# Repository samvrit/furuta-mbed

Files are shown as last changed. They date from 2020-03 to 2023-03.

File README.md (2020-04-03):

# Double Furuta Pendulum
The Furuta pendulum experiment is one that is used to teach advanced control theory concepts. The goal is to balance pendulum bar(s) upright by actuating a motor at the base.



This is a continuation of my masters' thesis project on the same topic, which can be found [here](https://drum.lib.umd.edu/bitstream/handle/1903/21255/Srinivas_umd_0117N_19182.pdf?sequence=1&isAllowed=y)

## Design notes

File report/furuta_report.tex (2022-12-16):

\documentclass{report}

\usepackage{geometry}
\usepackage{amsmath}
\usepackage{graphicx}
\usepackage{url}

\renewcommand{\bibname}{References}

\graphicspath{ {./images/} }

\title{Furuta Pendulum Control Project Report}

\author{Samvrit Srinivas}

\date{\today}

\begin{document}

\maketitle

\chapter{Motor Controller} \label{chap:motor_controller}

The input for the furuta pendulum is a torque applied by the motor at the base of the setup. The high-level controller computes the amount of torque to be applied by the motor, and the low-level controller runs a PI control on the torque reference. We use a DC brushed motor for this purpose, and hence the motor controller is designed to be a current controller, as the torque is directly proportional to the winding current. The winding current is controlled by applying a pulse-width-modulated voltage at the motor terminals. In the following sections, we will look into the mathematical model and the control design of the current/torque controller.

\section{Motor Selection and Parameter Derivation}	\label{sec:motor_selection}
By simulating the high level controller with slightly different initial conditions, we were able to get an idea of the torque and speed requirements of the DC motor. A motor with a stall-torque rating of at least 4 Nm and a speed rating of at least 60 RPM was deemed necessary. A motor from Pololu was selected with the nameplate specifications shown in Table \ref{table:pololu_specs} \cite{pololu_motor_specs}.

\begin{table}
\begin{center}
\begin{tabular}{|c|c|}
\hline
\textbf{Parameter} & \textbf{Value }\\
\hline\hline
Voltage & 12V \\
\hline
No-load speed & 67 RPM \\
\hline
No-load current & 0.2 A \\
\hline
Stall torque & 4.9 Nm \\
\hline
Stall current & 5.5 A \\
\hline
\end{tabular}
\caption{Pololu motor nameplate specifications} \label{table:pololu_specs}
\end{center}
\end{table}

From the nameplate specifications and from CAD drawings provided by the manufacturer, the other motor parameters were derived, as shown in Table \ref{table:pololu_motor_params}.

\begin{table}
\begin{center}
\begin{tabular}{|c|c|c|}
\hline
\textbf{Parameter} & \textbf{Value} & \textbf{Units} \\
\hline \hline
$K_t$ & $0.968$ & $Nm/A$ \\
\hline
$K_v$ & $1.7103$ & $V/rad/s$ \\
\hline
$L$ & $2.3e-3$ & $H$ \\
\hline
$R$ & $2.18$ & $\Omega$ \\
\hline
$J$ & $12e-9$ & $kgm^2$ \\
\hline
$b$ & $0.0151$ & $Nm/rad/s$ \\
\hline
\end{tabular}
\caption{Motor parameters} \label{table:pololu_motor_params}
\end{center}
\end{table}

\subsection{Parameter Derivations}

\subsubsection{Torque Constant ($K_t$)}
\begin{equation}
K_t = \frac{\text{stall-torque}}{\text{stall-current}}
\end{equation}

\subsubsection{Back-EMF Constant ($K_v$)}
\begin{equation}
K_v = \frac{\text{nameplate voltage}}{\text{nameplate speed}}
\end{equation}

\subsubsection{Winding Inductance ($L$) and Resistance ($R$)}
\begin{equation}
R = \frac{\text{nameplate voltage}}{\text{stall current}}
\end{equation}
The inductance was provided by the manufacturer. It is also possible to measure the inductance using an LCR meter.

\subsubsection{Rotor Inertia ($J$)}
From the CAD model, the dimensions (volume and length) of the rotor were obtained. Assuming that the rotor is made of stainless steel, and using the density for stainless steel as $\rho = 7,500 kg/m^3$, the mass was determined. Using mass and length, the rotor inertia was estimated using
\begin{equation}
J = \frac{1}{12} \cdot m \cdot l^2
\end{equation}

\subsubsection{Coefficient of Viscous Friction ($b$)}
\begin{equation}
b = \frac{\text{no-load-current} \cdot K_t}{\text{no-load-speed}}
\end{equation}

\section{Mathematical Model of DC Motor}	\label{sec:math_model}

Since the winding current is controlled by applying a certain voltage at the motor terminals, it is beneficial to look at the transfer function $\frac{I(s)}{V(s)}$. Figure \ref{fig:dc_motor_transfer_fn} represents the current-voltage dynamics of a DC motor \cite{motor_control_umich_lecture}:\\

\begin{figure}[h]
\centering
	
\caption{Motor transfer function}
\label{fig:dc_motor_transfer_fn}
\end{figure}

The combined transfer function is as follows:

\begin{align}
\frac{I\left(s\right)}{V\left(s\right)} &= \frac{sJ + b}{(sL + R)\cdot(sJ + b) + K_t \cdot K_v} \label{eq:motor_plant_transfer_fn} \\
\nonumber \\
\text{where,} \nonumber \\
I(s) &= \text{winding current} \nonumber \\
V(s) &= \text{terminal voltage} \nonumber \\
K_t &= \text{torque constant} \nonumber \\
K_v &= \text{back emf constant} \nonumber \\
J &= \text{rotor inertia} \nonumber\\
b &= \text{rotor friction-damping} \nonumber \\
L &= \text{winding inductance} \nonumber \\
R &= \text{winding resistance} \nonumber \\
V_b &= \text{back emf} \nonumber \\
\omega &= \text{rotor angular velocity} \nonumber \\
\tau &= \text{torque} \nonumber
\end{align}

Equation \ref{eq:motor_plant_transfer_fn} represents the plant dynamics for the controller that we wish to design.

\section{Motor Controller Design and Analysis}	\label{sec:motor_control_analysis}

The winding current is controlled by applying an appropriate pulse-width-modulated (PWM) voltage ($V_t$) at the motor terminals. The duty cycle of the PWM is calculated by a PI control loop using the current sense as feedback. We shall consider the load disturbance ($d$) and measurement noise ($n$) to analyze the disturbance rejection and noise sensitivity of the controller. We shall look at the bode plots and step responses of the gang of four transfer functions \cite{gang_of_four}.

\begin{figure}
\centering
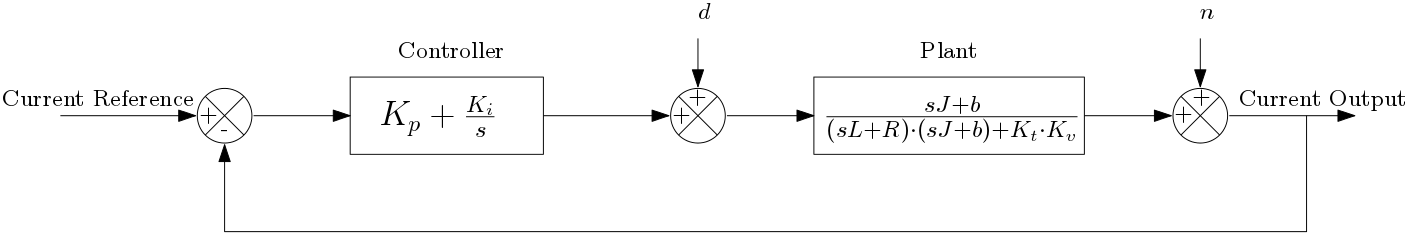
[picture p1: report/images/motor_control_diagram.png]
	
\caption{Current control diagram}
\label{fig:motor_control_diagram}
\end{figure}

\subsection{Plant Characteristics}
Figures \ref{fig:motor_plant_bode} and \ref{fig:motor_plant_step_response} show the plant characteristics without the influence of a controller.
\subsubsection{Transfer Function}
\begin{equation}
\frac{I(s)}{V(s)} = \frac{1.2e-08 s + 0.0151}{2.76e-11 s^2 + 3.476e-05 s + 1.688}
\end{equation}

\begin{figure}[h]
\centering
	
\caption{Bode plot of the motor transfer function}
\label{fig:motor_plant_bode}
\end{figure}

\begin{figure}[h]
\centering
	
\caption{Step response of the motor transfer function. Rise time = $8e-3$ seconds, settling time = $8.8e-3$ seconds}
\label{fig:motor_plant_step_response}
\end{figure}

\subsection{Closed Loop Characteristics}
Figures \ref{fig:motor_closed_loop_bode} and \ref{fig:motor_closed_loop_step_response} show the closed loop characteristics with PI control loop.
\subsubsection{Transfer Function}
\begin{equation}
\frac{I(s)}{I_{ref}(s)} = \frac{1.543e-17 s^5 + 3.962e-11 s^4 + 2.735e-05 s^3 + 2.47 s^2 + 5.999e04 s}{7.618e-22 s^6 + 1.934e-15 s^5 + 1.341e-09 s^4 + 1.447e-4 s^3 + 5.321 s^2 + 5.999e04 s}
\end{equation}

\begin{figure}[h]
\centering
	
\caption{Bode plot of the closed loop transfer function}
\label{fig:motor_closed_loop_bode}
\end{figure}

\begin{figure}[h]
\centering
	
\caption{Step response of the closed loop transfer function. Time to reach 66\% = $5.22e-5$ seconds, time to reach 90\% = $1.07e-4$ seconds }
\label{fig:motor_closed_loop_step_response}
\end{figure}

\subsection{Noise Sensitivity Characteristics}
Figures \ref{fig:motor_noise_sensitivity_bode} and \ref{fig:motor_noise_sensitivity_step_response} show the noise sensitivity characteristics. We can see that low frequency noise is well-attenuated, and a step in noise is short-lived (about $1e-4$ seconds).
\subsubsection{Transfer Function}
\begin{equation}
\frac{I(s)}{N(s)} = \frac{2.76e-11 s^3 + 3.476e-05 s^2 + 1.688 s}{2.76e-11 s^3 + 3.532e-05 s^2 + 2.42 s + 3.553e04}
\end{equation}

\begin{figure}[h]
\centering
	
\caption{Bode plot of the noise sensitivity transfer function}
\label{fig:motor_noise_sensitivity_bode}
\end{figure}

\begin{figure}[h]
\centering
	
\caption{Step response of the noise sensitivity transfer function}
\label{fig:motor_noise_sensitivity_step_response}
\end{figure}

\bibliographystyle{plain} 
\bibliography{furuta_bib}

\end{document}

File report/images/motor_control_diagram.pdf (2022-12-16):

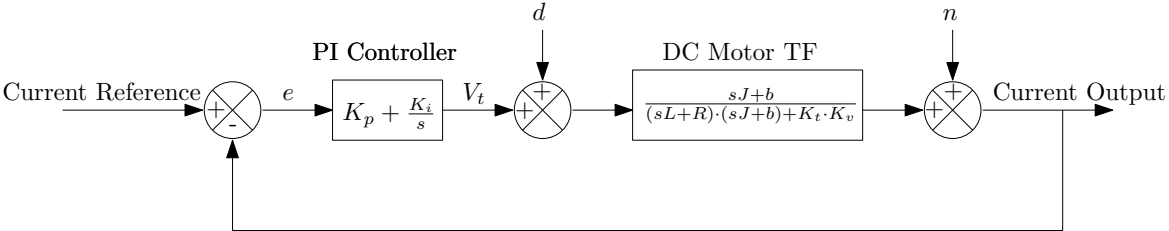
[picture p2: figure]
PI Controller; DC Motor TF Current Reference; Current Output +; PI Controller e

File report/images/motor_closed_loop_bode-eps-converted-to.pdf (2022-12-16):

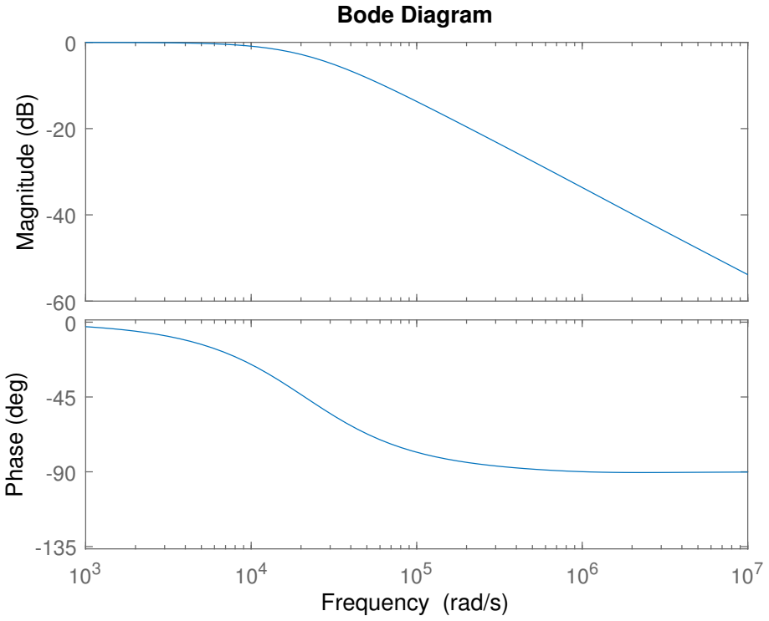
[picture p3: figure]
Magnitude (dB); Phase (deg); Bode Diagram; Frequency (rad/s)

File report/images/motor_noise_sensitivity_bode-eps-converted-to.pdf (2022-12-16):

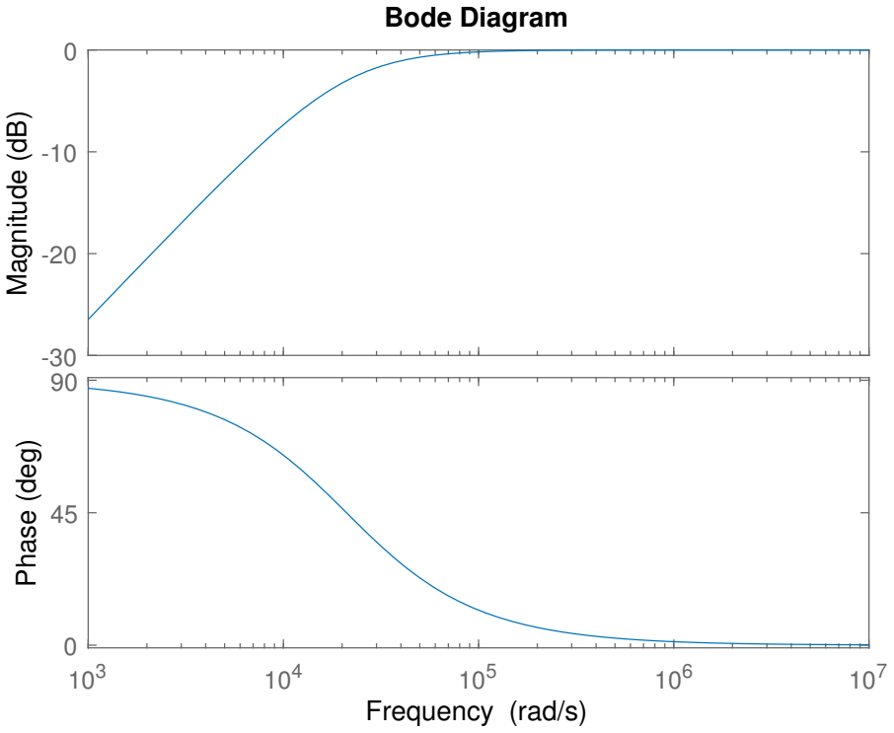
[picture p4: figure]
Magnitude (dB); Phase (deg); Bode Diagram; Frequency (rad/s)

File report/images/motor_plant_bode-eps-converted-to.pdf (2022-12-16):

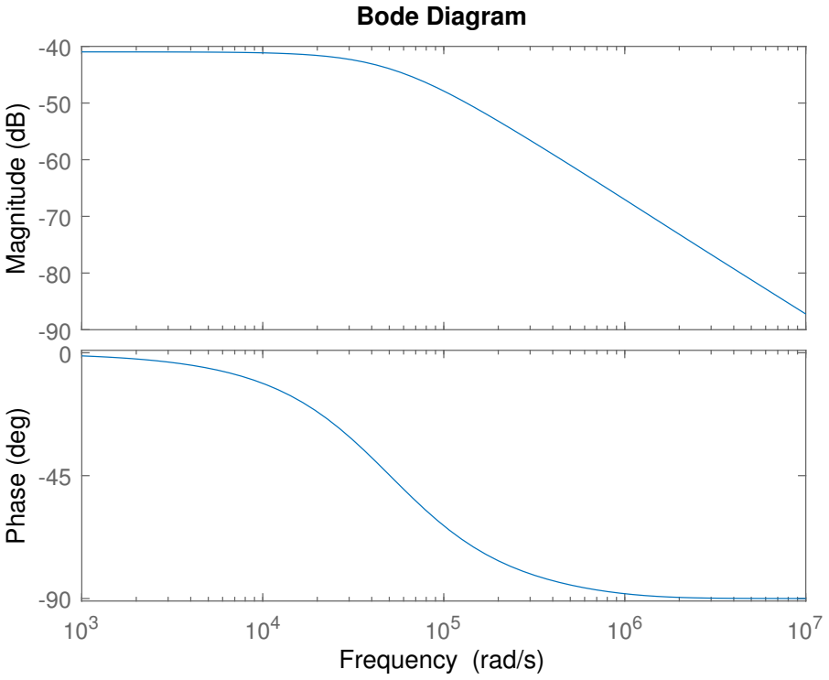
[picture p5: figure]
Magnitude (dB); Phase (deg); Bode Diagram; Frequency (rad/s)

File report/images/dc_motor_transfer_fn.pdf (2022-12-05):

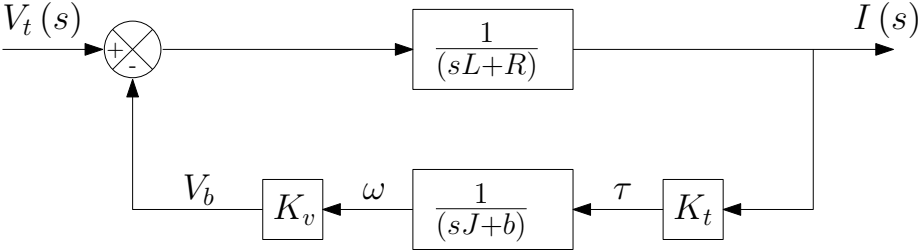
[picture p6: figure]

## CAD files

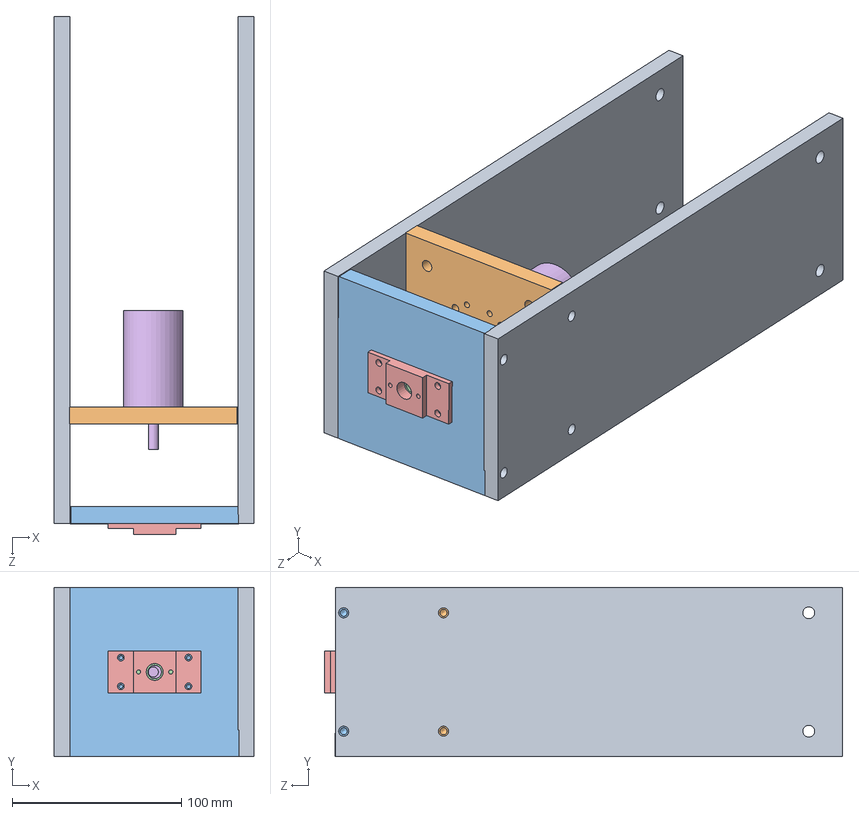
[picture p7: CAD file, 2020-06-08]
solids/base/Assembly_base.SLDASM
118.3 x 100.0 x 306.4 mm
mount-sides x 2
mount-motor
mount-top
bearing
encoder-mount-1
motor

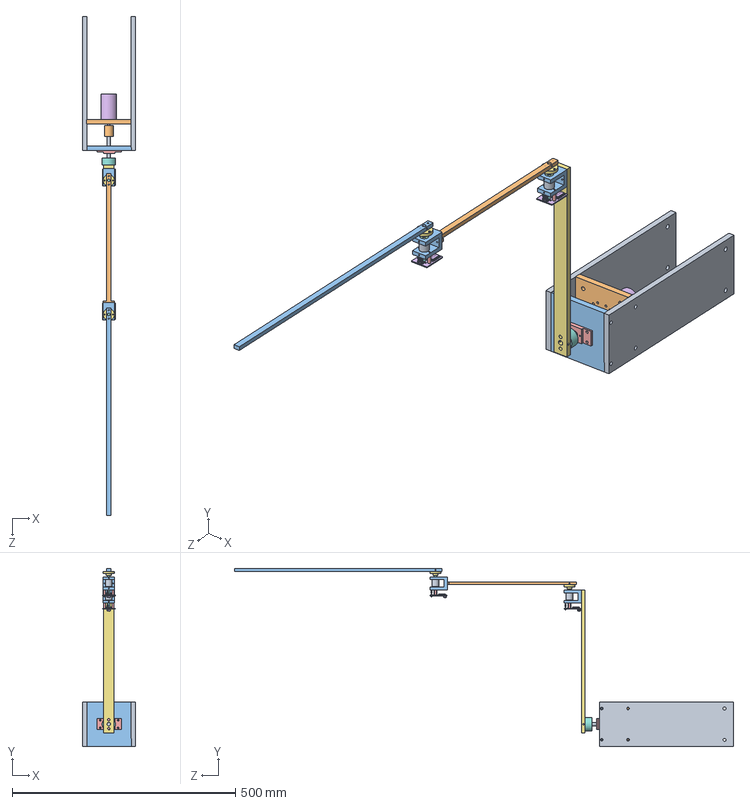
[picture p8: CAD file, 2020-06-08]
solids/Complete_assembly.SLDASM
118.3 x 398.4 x 1117.0 mm
mount-sides x 2
mount-motor
mount-top
bearing
encoder-mount-1
motor
link-1
shaft-collar-8mm
shaft-1
coupling-6mm-8mm
bearing-mount-1 x 2
bearing-6mm x 4
pcb-standoffs x 4
position-sensor-pcb x 2
hub x 2
pin-encoder x 4
coupling-6mm x 2
link-2
link-3

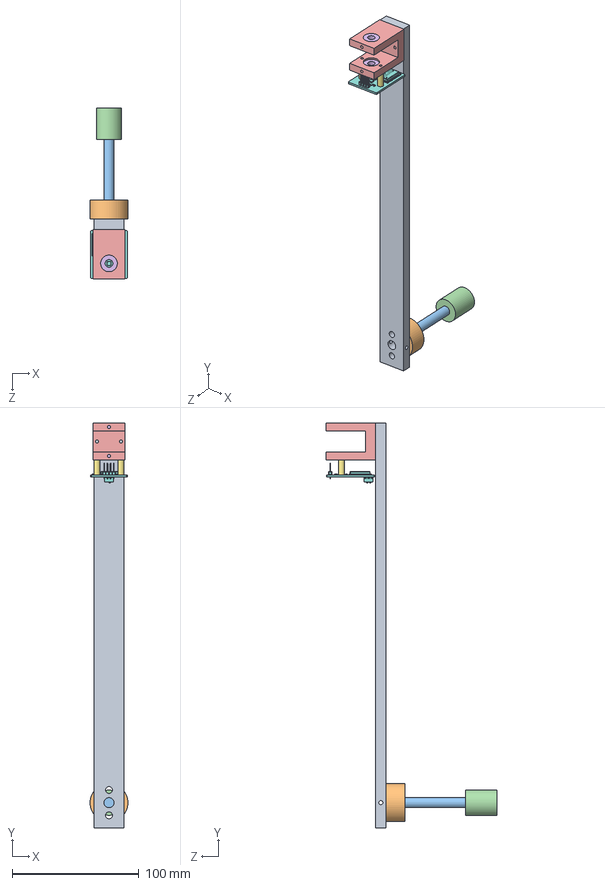
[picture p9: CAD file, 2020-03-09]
solids/link1/Assembly_link1.SLDASM
30.0 x 320.0 x 135.5 mm
link-1
shaft-collar-8mm
shaft-1
coupling-6mm-8mm
bearing-mount-1
bearing-6mm x 2
pcb-standoffs x 2
position-sensor-pcb

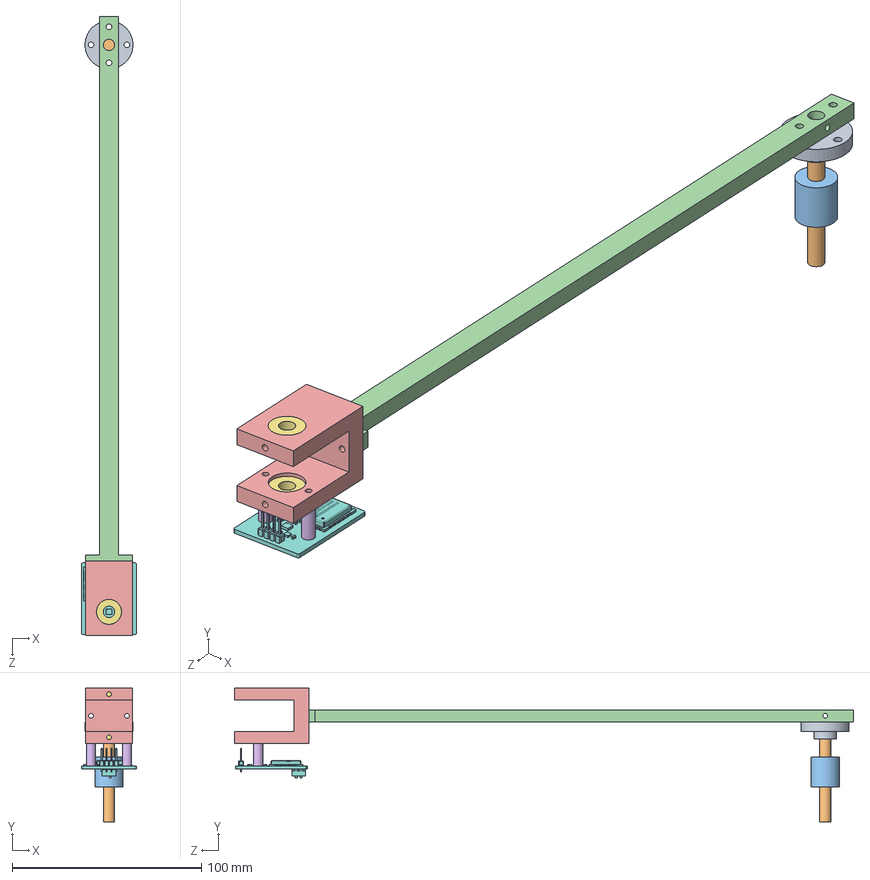
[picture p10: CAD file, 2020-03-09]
solids/link2/Assembly_link2.SLDASM
29.1 x 70.7 x 327.5 mm
hub
pin-encoder x 2
coupling-6mm
link-2
bearing-mount-1
pcb-standoffs x 2
bearing-6mm x 2
position-sensor-pcb

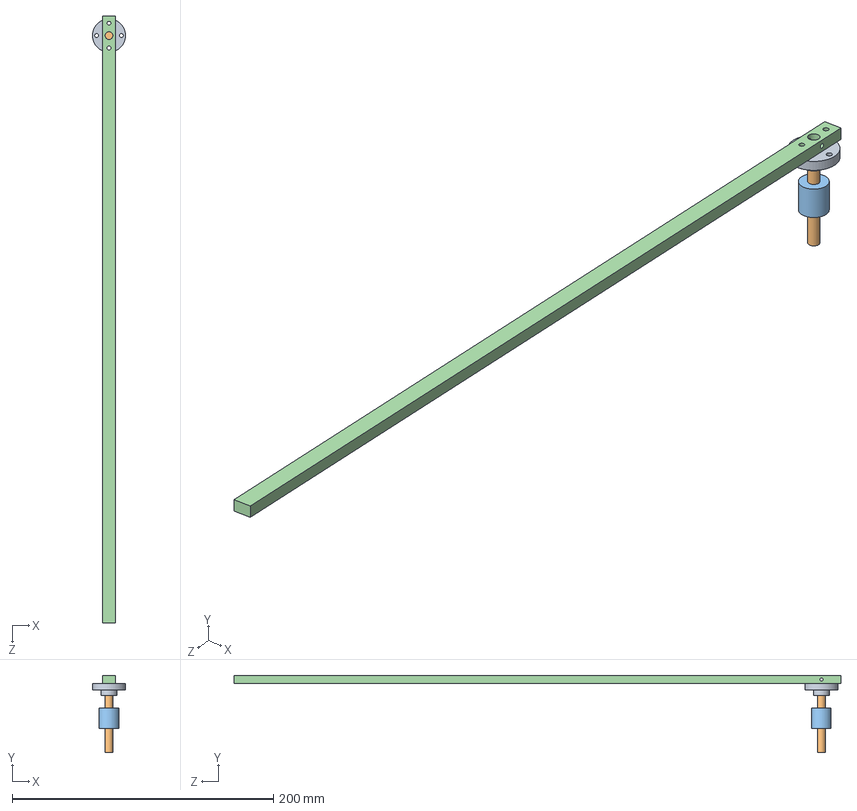
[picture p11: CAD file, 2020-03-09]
solids/link3/Assembly_link3.SLDASM
25.4 x 59.2 x 465.0 mm
hub
pin-encoder x 2
coupling-6mm
link-3

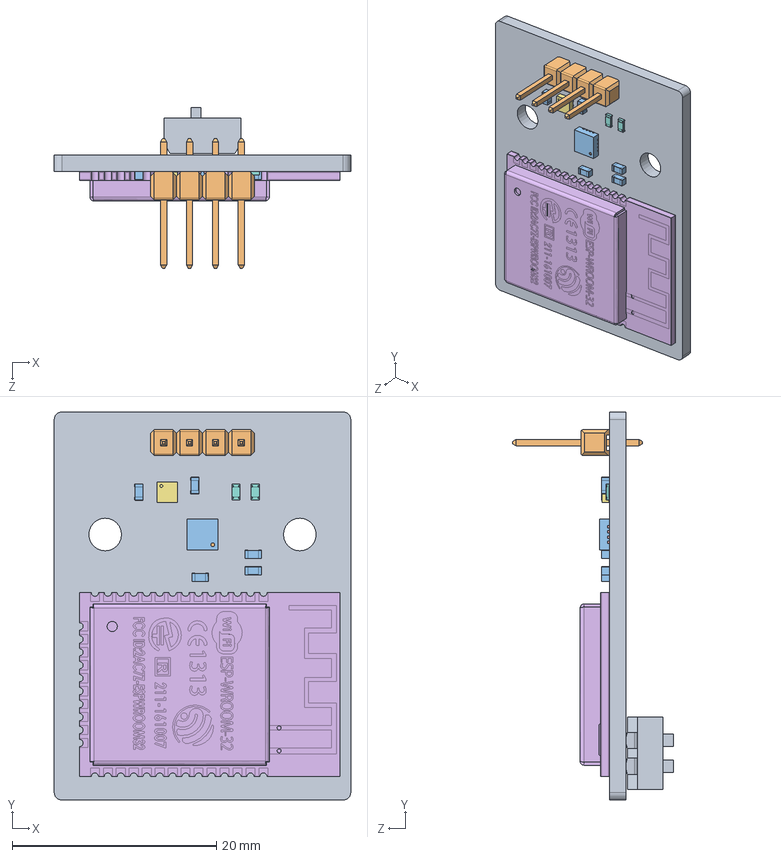
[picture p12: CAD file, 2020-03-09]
solids/common/pcb-assembly.SLDASM
29.1 x 38.0 x 15.7 mm
Open_CASCADE_STEP_translator_6.8_2.1
Open_CASCADE_STEP_translator_6.8_2.2.1
Thermal_Shape
Open_CASCADE_STEP_translator_6.8_2.4.1 x 16
User_Library-ESP321
User_Library-QFN6
SW3dPS-R0603 x 2
c-1825058-1-o-3d
User_Library-1x2_TH_Pitch_2_54mm x 2
MLCC_capacitor_0603_-_0.8mm x 5

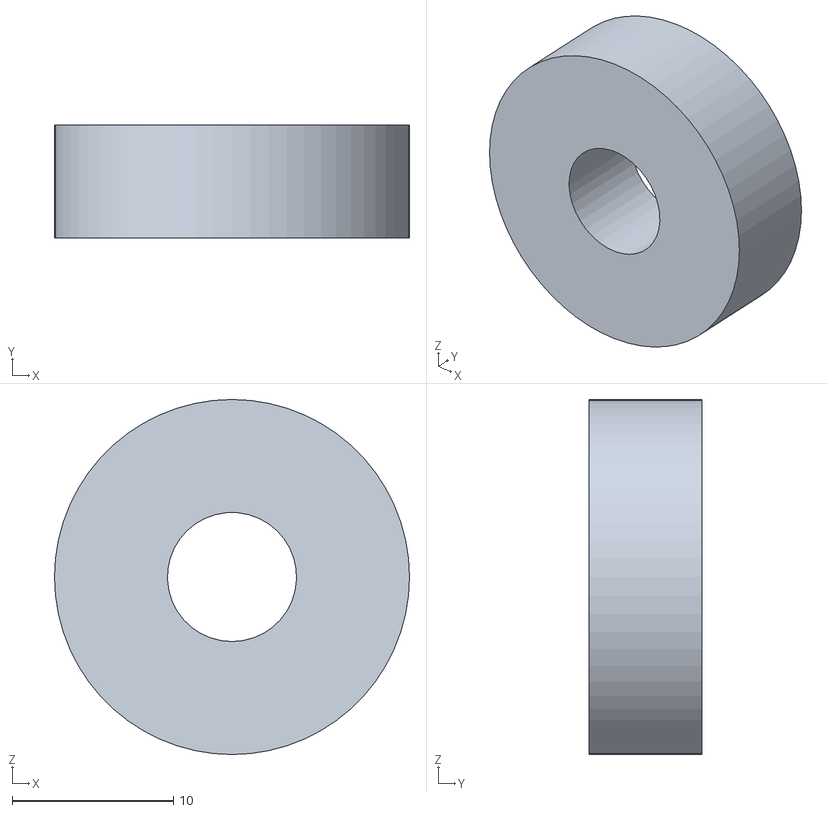
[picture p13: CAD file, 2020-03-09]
matlab/TwoLink/solidworks_model/bearing_Default_sldprt.STL
22.0 x 7.00 x 22.0

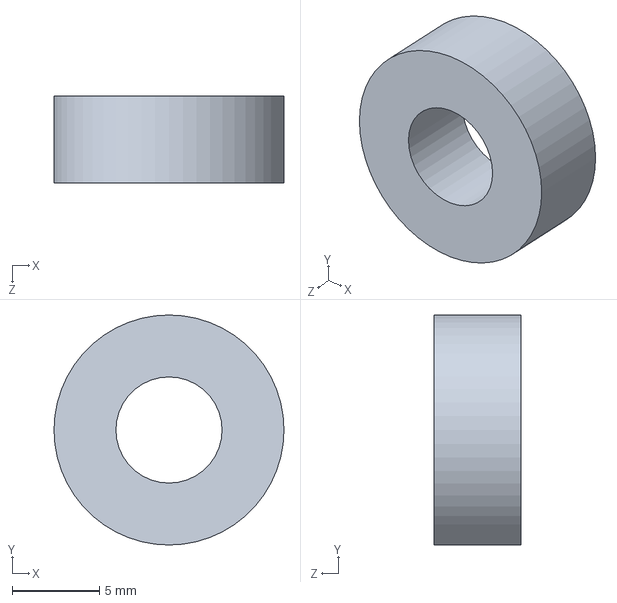
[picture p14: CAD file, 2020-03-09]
solids/common/bearing-6mm.SLDPRT
13.2 x 13.2 x 5.00 mm

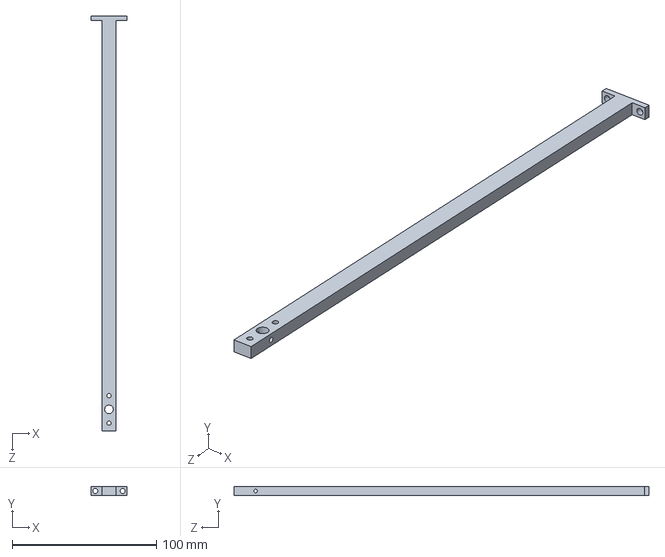
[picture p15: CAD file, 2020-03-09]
solids/link2/link-2.SLDPRT
25.0 x 6.35 x 288.0 mm

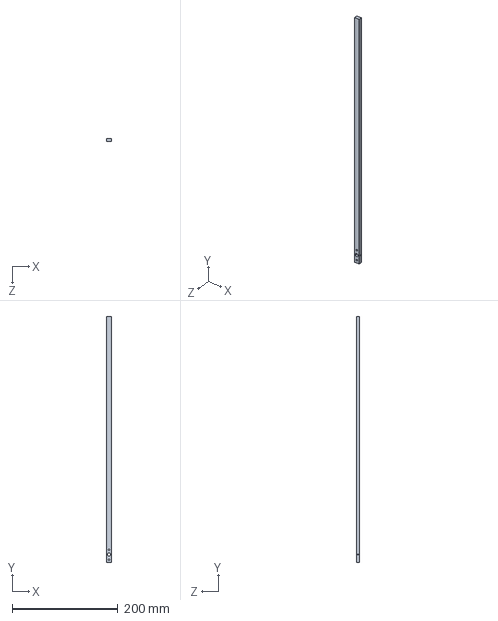
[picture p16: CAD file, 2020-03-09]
solids/link3/link-3.SLDPRT
10.0 x 465.0 x 6.35 mm

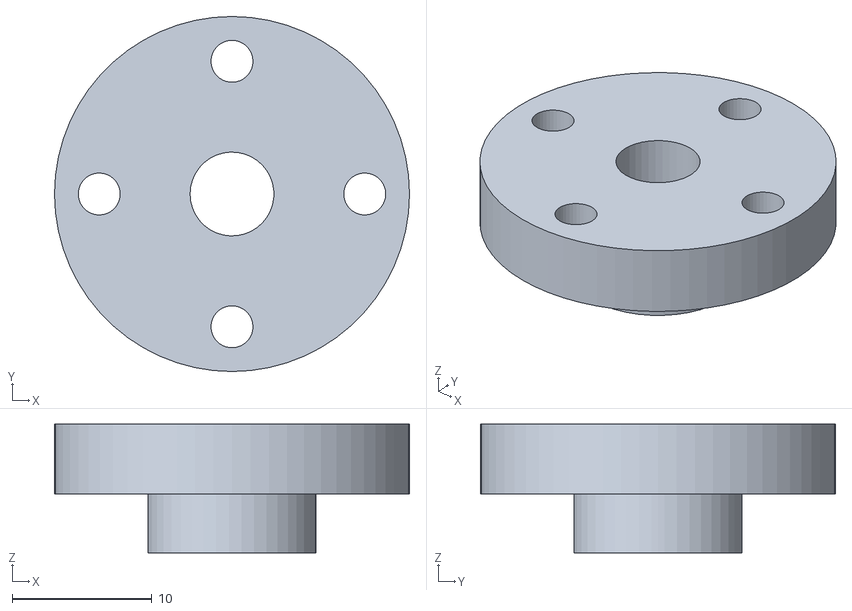
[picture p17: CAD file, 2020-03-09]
matlab/TwoLink/solidworks_model/hub_Default_sldprt.STL
25.4 x 25.4 x 9.20

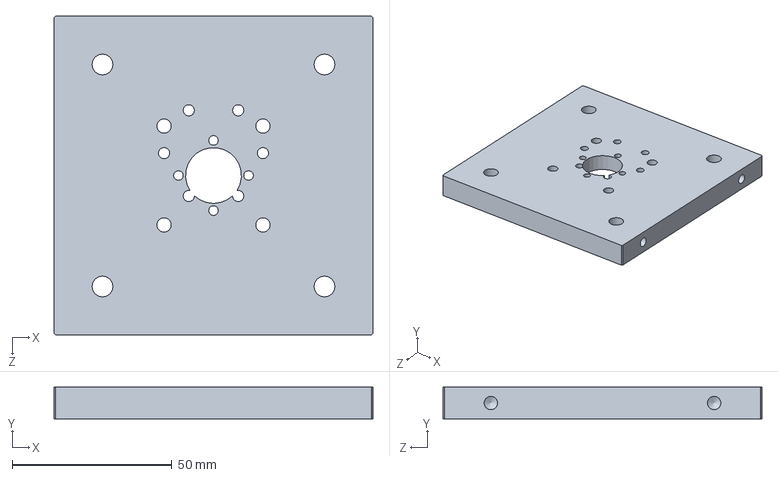
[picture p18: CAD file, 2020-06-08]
solids/base/mount-motor.SLDPRT
100.0 x 10.0 x 100.0 mm

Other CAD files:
motor_controller_ti/motor_controller/CPU1_FLASH/device/device.obj
motor_controller_ti/motor_controller/CPU1_RAM/asin.obj
motor_controller_ti/motor_controller/CPU1_RAM/device/F2837xD_CodeStartBranch.obj
motor_controller_ti/motor_controller/CPU1_FLASH/device/F2837xD_CodeStartBranch.obj
motor_controller_ti/motor_controller/CPU1_RAM/cla_ex1_asin.obj
motor_controller_ti/motor_controller/CPU1_RAM/device/device.obj
matlab/TwoLink/solidworks_model/bearing-6mm_Default_sldprt.STL
matlab/TwoLink/solidworks_model/bearing-mount-1_Default_sldprt.STL
matlab/TwoLink/solidworks_model/coupling-6mm-8mm_Default_sldprt.STL
matlab/TwoLink/solidworks_model/coupling-6mm_Default_sldprt.STL
matlab/TwoLink/solidworks_model/encoder-mount-1_Default_sldprt.STL
matlab/TwoLink/solidworks_model/link-1_Default_sldprt.STL
matlab/TwoLink/solidworks_model/link-2_Default_sldprt.STL
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

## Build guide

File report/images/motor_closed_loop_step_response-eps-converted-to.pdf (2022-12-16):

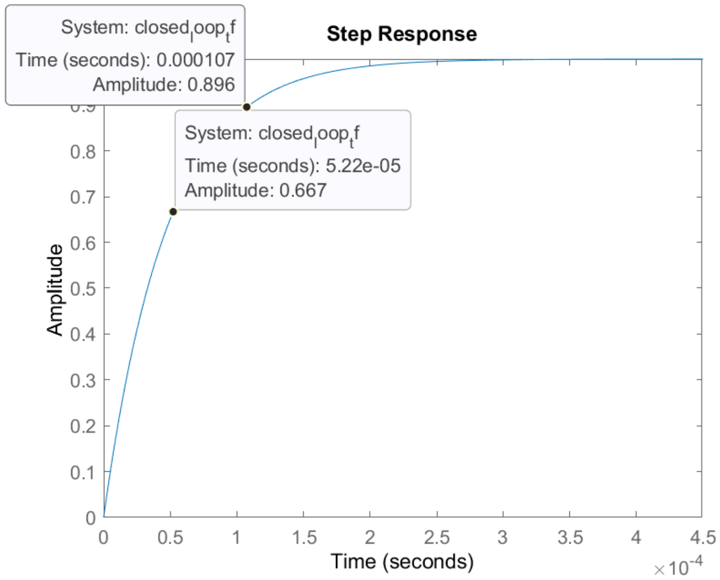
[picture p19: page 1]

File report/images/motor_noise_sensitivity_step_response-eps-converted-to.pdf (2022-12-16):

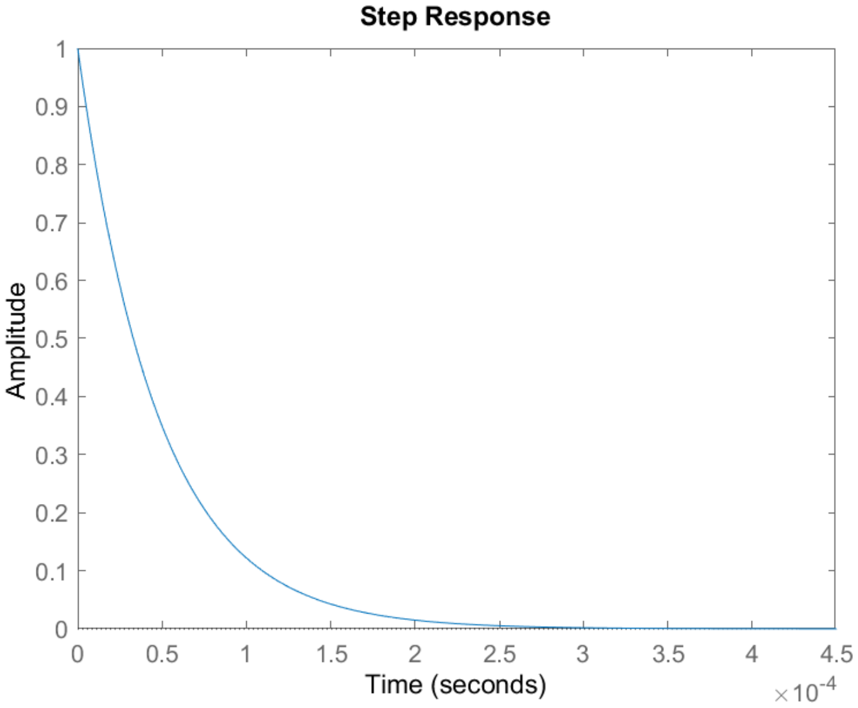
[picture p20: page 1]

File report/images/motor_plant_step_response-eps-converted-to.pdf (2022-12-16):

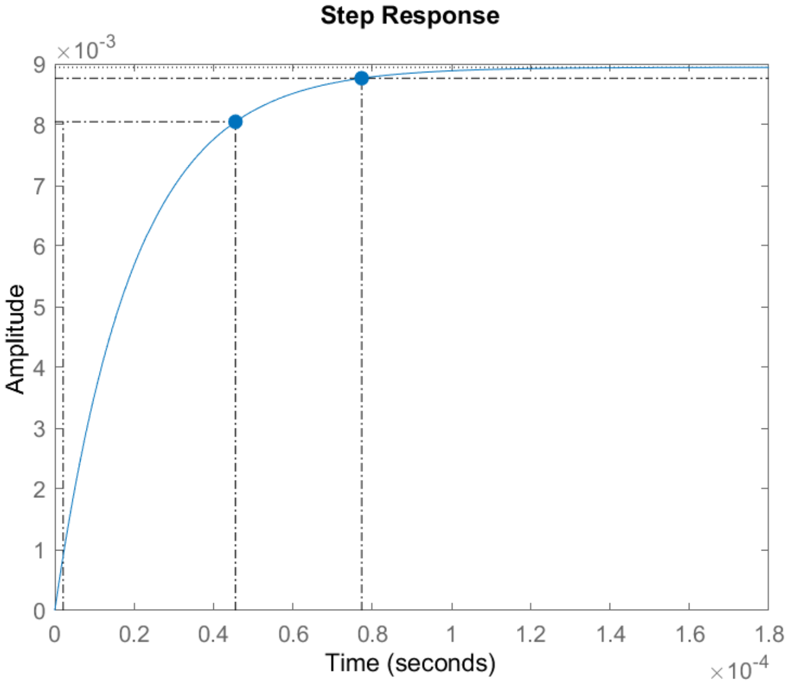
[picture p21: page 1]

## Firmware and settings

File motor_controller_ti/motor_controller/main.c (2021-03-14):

//###########################################################################
// $TI Release: F2837xD Support Library v3.09.00.00 $
// $Release Date: Thu Mar 19 07:35:24 IST 2020 $
// $Copyright:
// Copyright (C) 2013-2020 Texas Instruments Incorporated - http://www.ti.com/
//
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
//   Redistributions of source code must retain the above copyright 
//   notice, this list of conditions and the following disclaimer.
// 
//   Redistributions in binary form must reproduce the above copyright
//   notice, this list of conditions and the following disclaimer in the 
//   documentation and/or other materials provided with the   
//   distribution.
// 
//   Neither the name of Texas Instruments Incorporated nor the names of
//   its contributors may be used to endorse or promote products derived
//   from this software without specific prior written permission.
// 
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
/*==================INCLUDES==================*/
#include "driverlib.h"
#include "device.h"
#include "cla_shared.h"
#include "peripheral_initializations.h"
#include "globals.h"
#include "timer_inlines.h"
#ifndef TEST_MODE
#include "fpu_vector.h"
#endif //TEST_MODE

/*==================DEFINES==================*/
#define RLS_POSITION_SCALER     (2.0F * PI / 16384.0F)

/*==================VARIABLES==================*/

uint16_t rDataA[COMM_MSG_RECV_DATA_LENGTH];
float32_t x1 = 0.0F, x2 = 0.0F, x3 = 0.0F, x4 = 0.0F;
uint16_t wifiDataValid = 1U;
uint64_t wifiDataInvalidCount = 0U;
uint32_t timer_count = 0U;
uint16_t RLS_calibration_complete = 0U;
uint16_t crc = 0U;
uint16_t RLS_position_raw = 0U;
uint16_t RLS_position_status = 0U;

volatile interfacePacket_t uartPacket, canPacket, spiPacket;
volatile float32_t torqueCommand = 0.0F; // torque command as obtained from SCI
volatile uint16_t CAN_errorFlag = 0U;
volatile uint16_t setMotorPWMFlag = 0U;
volatile uint16_t getWiFiDataFlag = 0U;
volatile uint16_t getRLSDataFlag = 0U;

uint16_t motorDriverFaultCount; // indicates a fault in the motor driver


/*==================CLA VARIABLE DEFINITIONS==================*/
#pragma DATA_SECTION(claInputs,"CpuToCla1MsgRAM");
claInputs_S claInputs;
#pragma DATA_SECTION(claOutputs,"Cla1ToCpuMsgRAM");
claOutputs_S claOutputs;

/*==================FUNCTION PROTOTYPES==================*/
void setMotorPWM(float);
void getWiFiData(void);
void RLS_getData(void);
void RLS_triggerSelfCalibration(void);
void RLS_setZeroPositionOffset(uint16_t);


/*==================MAIN==================*/
void main(void)
{

    Device_init();                  // Intialize device clock and peripherals
    Device_initGPIO();              // Disable pin locks and enable internal pullups.
    Interrupt_initModule();         // Initialize PIE and clear PIE registers. Disables CPU interrupts
    Interrupt_initVectorTable();    // Initialize the PIE vector table with pointers to the shell Interrupt Service Routines (ISR).

    Interrupt_register(INT_ADCA1, &adcA1ISR);
    Interrupt_register(INT_SCIB_RX, &scibRXFIFOISR);
    Interrupt_register(INT_CLA1_1, &cla1Isr1);  // Configure the vectors for the end-of-task interrupt for task 1
    Interrupt_register(INT_CLA1_8, &cla1Isr8);  // Configure the vectors for the end-of-task interrupt for task 8
    Interrupt_register(INT_CANB0, &canISR);
    Interrupt_register(INT_TIMER0, &cpuTimer0ISR);
    Interrupt_register(INT_XINT1, &xint1_isr);  // push button input
    Interrupt_register(INT_XINT2, &xint2_isr);  // motor driver fault indication

    initSCIBFIFO();

    configCPUTimer(CPUTIMER0_BASE, CONTROL_CYCLE_TIME_US, 1);   // timer0 for control cycle
    configCPUTimer(CPUTIMER1_BASE, MAX_CPU_TIMER_PRD, 0);       // timer1 for getting counter value

    configGPIOS();

    SysCtl_disablePeripheral(SYSCTL_PERIPH_CLK_TBCLKSYNC);  // Disable sync(Freeze clock to PWM as well)
    initEPWM();
    SysCtl_enablePeripheral(SYSCTL_PERIPH_CLK_TBCLKSYNC);   // Enable sync and clock to PWM

    // Initialize CANB module
    CAN_initModule(CANB_BASE);
    CAN_setBitRate(CANB_BASE, DEVICE_SYSCLK_FREQ, 1000000, 20);

    CAN_enableInterrupt(CANB_BASE, CAN_INT_IE0 | CAN_INT_ERROR | CAN_INT_STATUS);   // Enable CANB interrupts

    // Initialize variables
    claInputs.enable = 0;
    claInputs.currentAmperes = 0.0;
    claInputs.torqueCommand = 0.0;

    // Configure the CLA memory spaces first followed by the CLA task vectors
    CLA_configClaMemory();
    CLA_initCpu1Cla();
    waitCount(5U * WAIT_COUNT_1_US); // 5 us to complete initializations in CLA task 8

    initADC();
    initADCSOC();

    // reset the motor driver sleep pin to get it to a known state, since it is an open-drain output
    GPIO_writePin(MOTOR_DRIVER_SLEEP_PIN, 0);
    waitCount(WAIT_COUNT_1_MS);    // 2 s
    GPIO_writePin(MOTOR_DRIVER_SLEEP_PIN, getMotorEnableFlag());

    // Enable CLA, ADC and SCI interrupts
    Interrupt_enable(INT_CLA1_1);
    Interrupt_enable(INT_CLA1_8);
    Interrupt_enable(INT_ADCA1);
    Interrupt_enable(INT_SCIB_RX);
    Interrupt_enable(INT_CANB0);
    Interrupt_enable(INT_XINT1);
    Interrupt_enable(INT_XINT2);
    Interrupt_enable(INT_TIMER0);

    CAN_enableGlobalInterrupt(CANB_BASE, CAN_GLOBAL_INT_CANINT0);

    //CANB setup message object
    CAN_setupMessageObject(CANB_BASE, CAN_RX_MSG_OBJ_ID, 0x1, CAN_MSG_FRAME_STD, CAN_MSG_OBJ_TYPE_RX, 0, CAN_MSG_OBJ_RX_INT_ENABLE, COMM_MSG_RECV_DATA_LENGTH);

    initSPIA();
    initSPIB();

    // Enable Global Interrupt (INTM) and realtime interrupt (DBGM)
    EINT;
    ERTM;

#ifdef RLS_TRIGGER_SELF_CALIBRATION
    RLS_calibration_complete = 0U;
    RLS_triggerSelfCalibration();
    RLS_calibration_complete = 1U;
#endif // RLS_TRIGGER_SELF_CALIBRATION

    // calibrate ADC zero bias -- this is done because at every startup, the zero bias seems to vary
    setADCCalibratedFlag(0U);                           // set ADC-calibrated flag explicitly to avoid motor getting enabled
    while(!isLVPowerPresent());                         // wait till 3.3V is present so that the current sensor is powered
    waitCount(2U * WAIT_COUNT_1_S);                     // wait for LPF to settle
    setADCZeroBias((uint16_t)getADCResultRawLPF());     // latch the instantaneous zero-current ADC value to the ADC zero bias
    setADCCalibratedFlag(1U);                           // set ADC-calibrated flag to true

    for(;;)
    {
        if(setMotorPWMFlag)
        {
            setMotorPWM(uartPacket.value);
            setMotorPWMFlag = 0U;
        }

        if(getWiFiDataFlag)
        {
            getWiFiData();
            getWiFiDataFlag = 0U;
        }

        if(getRLSDataFlag)
        {
            startTimerCounter();
            RLS_getData();
            timer_count = getTimerCounter();
            resetTimerCounter();
            getRLSDataFlag = 0U;
        }

    }
}

void setMotorPWM(float PWM_dutyCycle)
{
    ASSERT(PWM_dutyCycle <= 1.0F);

    uint32_t PWM_newCMPA = EPWM1_TIMER_TBPRD - (uint16_t)ABS(PWM_dutyCycle * EPWM1_TIMER_TBPRD);         // compute new Compare A register value
    uint32_t motor_direction = PWM_dutyCycle > 0.0 ? 1 : 0;   // set direction

    EPWM_setCounterCompareValue(EPWM1_BASE, EPWM_COUNTER_COMPARE_A, PWM_newCMPA);
    GPIO_writePin(MOTOR_DRIVER_DIRECTION_PIN, motor_direction);
}

void getWiFiData(void)
{
    int i;
    // write 0x00 9 times to transfer 72 bits
#pragma UNROLL(9)
    for(i = 0; i < 9; i++)
    {
        SPI_writeDataBlockingNonFIFO(SPIA_BASE, 0x00);
    }

    while(SPI_getRxFIFOStatus(SPIA_BASE) != SPI_FIFO_RX9){};    // wait until 9 words have been received from wifi device

    // first get x2 by reading from FIFO buffer
    spiPacket.buffer[0] = (SPI_readDataBlockingFIFO(SPIA_BASE) << 8) | SPI_readDataBlockingFIFO(SPIA_BASE);
    spiPacket.buffer[1] = (SPI_readDataBlockingFIFO(SPIA_BASE) << 8) | SPI_readDataBlockingFIFO(SPIA_BASE);
    x2 = spiPacket.value;

    // then get x3
    spiPacket.buffer[0] = (SPI_readDataBlockingFIFO(SPIA_BASE) << 8) | SPI_readDataBlockingFIFO(SPIA_BASE);
    spiPacket.buffer[1] = (SPI_readDataBlockingFIFO(SPIA_BASE) << 8) | SPI_readDataBlockingFIFO(SPIA_BASE);
    x3 = spiPacket.value;

    // in the end, get the byte that indicates if the data is valid or not
    wifiDataValid = SPI_readDataBlockingFIFO(SPIA_BASE);

    if(wifiDataValid != 3U) wifiDataInvalidCount++;

    SPI_resetRxFIFO(SPIA_BASE); // reset receive buffer
}

void RLS_getData(void)
{
    const uint16_t data_request_command[2] = {0x0000, 0x0000};
    int i;

#pragma UNROLL(2)
    for(i = 0; i < 2; i++)
    {
        SPI_writeDataBlockingNonFIFO(SPIB_BASE, data_request_command[i]);
    }

    while(SPI_getRxFIFOStatus(SPIB_BASE) != SPI_FIFO_RX2){};    // wait until 3 words have been received from RLS sensor

    /* reply frame looks like this:
    b24:b10 = position data (14-bit)
    b9:b8 = status bits
    b7:b0 = crc
    */

    // first read position and status
    uint16_t pos_status = SPI_readDataBlockingFIFO(SPIB_BASE);
    RLS_position_raw = (pos_status & 0xFFFC) >> 2;
    RLS_position_status = pos_status & 0x03;
    x1 = ((float)RLS_position_raw) * RLS_POSITION_SCALER;

    // then read crc
    crc = SPI_readDataBlockingFIFO(SPIB_BASE) >> 8;

    SPI_resetRxFIFO(SPIB_BASE); // reset receive buffer
}

void RLS_triggerSelfCalibration(void)
{
    const uint16_t self_calib_sequence[5] = {0xCD00, 0xEF00, 0x8900, 0xAB00, 0x4100};
    int i;

    setMotorPWM(0.05F);  // 20% duty cycle
    waitCount(2U * WAIT_COUNT_1_S);  // 2 s

    SPI_resetTxFIFO(SPIB_BASE);

    for(i = 0; i < 5; i++)
    {
        SPI_writeDataBlockingFIFO(SPIB_BASE, self_calib_sequence[i]);
        waitCount(20U * WAIT_COUNT_1_US);    // 100 us
    }

    waitCount(10U * WAIT_COUNT_1_S);  // 10 s
    setMotorPWM(0.0F);
}

void RLS_setZeroPositionOffset(uint16_t position_offset)
{

}

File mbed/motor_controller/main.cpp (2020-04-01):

/*=======================INCLUDES========================*/
#include "mbed.h"
#include "PwmIn.h"

/*=======================DEFINES========================*/
#define PI 3.14F
#define MICROSECOND 0.000001F

#define GEARBOX_RATIO 30.0F
#define ROTATION_PER_PULSE (2.0F * PI / (16.0F * GEARBOX_RATIO))  // radians per pulse
#define MOTOR_SPEED_THRESHOLD_RAD_S 50000.0F

#define CURRENT_LPF_CUTOFF_FREQ_HZ 3500U    // cutoff frequency for low pass filter
#define CURRENT_SENSE_OFFSET 0.091F         // ADC value when 0 current is present
#define CURRENT_SENSE_SCALING_FACTOR 13.73F // calculated by considering rate of change of voltage w.r.t. current, as well as voltage divider circuit (5V -> 3V)
#define CURRENT_SENSE_LOWER_BOUND 0.0F
#define CURRENT_SENSE_UPPER_BOUND 10.0F
#define MOTOR_CONSTANT_KT 0.2525F           // Nm/A

#define KP 166.08F                          // proportional gain for PI controller
#define KI 26161.30F                        // integral gain for PI controller

#define DUTY_CYCLE_LOWER_BOUND 0.0F
#define DUTY_CYCLE_UPPER_BOUND 1.0F
#define MOTOR_PWM_FREQUENCY_US 50.0F

#define SATURATE(input, lower_limit, upper_limit) ((input) > (upper_limit) ? (upper_limit) : ((input) < (lower_limit) ? (lower_limit) : (input)))
#define LOW_PASS_FILTER(output, input, dt, cutoff_freq) ((output) += (((input) - (output)) * 2 * PI * (cutoff_freq) * (dt) * MICROSECOND))
#define ABS(input) ((input) < 0 ? -(input) : (input))

/*=======================PERIPHERALS========================*/
DigitalOut motorEnable(PA_8);               // 3.3V power source for gate driver IC
PwmOut motorPWM(PA_5);                      // PWM for gate driver IC
DigitalOut inA(PA_6);                       // direction pin A
DigitalOut inB(PA_7);                       // direction pin B
AnalogIn currentSenseExternal(PA_4);        // current sense analog input
AnalogIn currentSenseDriver(PB_0);          // current sense from the motor driver
PwmIn encoder(PB_6);                        // encoder input

InterruptIn buttonPress(BUTTON1, PullDown);                // button for motor enable/disable

Timer t;                                    // timer for calculating code execution rate

RawSerial torqueInput(PA_0, PA_1);         // serial communication for getting torque commands

/*=======================STRUCTS & UNIONS========================*/
// use a union to decode float packet received through UART
typedef union {
    float value;
    char buffer[sizeof(float)];
} uartPacket_t;

typedef struct {
    bool motorEnabled = false;              // flag for when motor is enabled using button
    bool torqueCommandAvailable = false;    // flag for when new torque command is available
} flags_t;

/*=======================VOLATILES========================*/
volatile char rx_buffer[sizeof(float) + 1]; // receive buffer for UART packet containing torque command
volatile int rx_count;                      // index for receive buffer byte array
volatile flags_t flags;
volatile uartPacket_t uartPacket;

/*=======================INTERRUPT HANDLERS========================*/
// Interrupt service routine for when user button is pressed for enabling/disabling motor driver
void flip(void)
{
    flags.motorEnabled = !flags.motorEnabled;
}

// Interrupt service routine for UART RX
void rx_irq(void)
{
    while(torqueInput.readable())
    {
        rx_buffer[rx_count] = torqueInput.getc();  // fill available byte into buffer
        if(rx_buffer[rx_count] == '\r')             // look for carriage return
        {
            flags.torqueCommandAvailable = true;
            rx_count = 0;                           // reset buffer index
            break;
        }
        else
        {
            rx_count++;                             // increment index counter
        }
    }
}

/*=======================MAIN========================*/
int main()
{
    torqueInput.baud(115200);                          // set UART baud rate
    torqueInput.attach(&rx_irq, RawSerial::RxIrq);

    torqueInput.printf("Hello World!\n");

    buttonPress.rise(&flip);

    inA = 1;
    inB = 0;

    float dutyCycle = 0.0;
    float currentSenseLPF = 0.0;
    float currentSenseRaw = 0.0;
    float torqueCommand = 0.02;
    float torqueFeedback = 0.0;
    float torqueError = 0.0;
    float torqueErrorIntegral = 0.0;
    int executionRate_ms = 0;

    float motorSpeed = 0.0;
    float dt = 1;

    motorPWM.period_us(MOTOR_PWM_FREQUENCY_US); // set PWM frequency to 100 microseconds (10 kHz)
    
    while(true)
    {
        if(flags.torqueCommandAvailable)
        {
            NVIC_DisableIRQ(UART4_IRQn);    // disable UART interrupt while processing new information
            memcpy((void *)&uartPacket.buffer, (void *)&rx_buffer, sizeof(float));  // write buffer contents into union variable
            memset((void *)&rx_buffer, 0, sizeof(float) + 1);   // clear rx buffer
            NVIC_EnableIRQ(UART4_IRQn);     // enable UART interrupt after processing new torque command
            torqueInput.printf("New torque command: %f, dt: %d, motor speed: %f\n", uartPacket.value, executionRate_ms, motorSpeed);
            torqueCommand = uartPacket.value;
            flags.torqueCommandAvailable = false;
        }
        
        if(flags.motorEnabled && (motorSpeed < MOTOR_SPEED_THRESHOLD_RAD_S))
        {
            t.start();
            motorEnable = 1;   // 3.3V power source for gate driver IC
            
            currentSenseRaw = ABS(currentSenseExternal.read() - CURRENT_SENSE_OFFSET) * CURRENT_SENSE_SCALING_FACTOR; // current sense in amperes
            currentSenseRaw = SATURATE(currentSenseRaw, CURRENT_SENSE_LOWER_BOUND, CURRENT_SENSE_UPPER_BOUND);
            LOW_PASS_FILTER(currentSenseLPF, currentSenseRaw, executionRate_ms, CURRENT_LPF_CUTOFF_FREQ_HZ); // apply low pass filter

            torqueFeedback = MOTOR_CONSTANT_KT * currentSenseLPF;   // calculate output torque (tau = Kt * i)
            torqueError = ABS(torqueCommand) - torqueFeedback;   // compute error signal
            torqueErrorIntegral += torqueError; // compute integral of error signal

            dutyCycle = (KP * torqueError) + (KI * torqueErrorIntegral);   // PI controller
            dutyCycle = SATURATE(dutyCycle, DUTY_CYCLE_LOWER_BOUND, DUTY_CYCLE_UPPER_BOUND);  // saturate duty cycle

            inA = torqueCommand < 0 ? 0 : 1;    // set direction
            inB = !inA;
            motorPWM.write(dutyCycle);    // set duty cycle

            dt = encoder.period();                  // find time difference between two encoder pulses
            motorSpeed = (dt == 0.0) ? 0.0 : (ROTATION_PER_PULSE / dt); // don't divide by zero
            
            executionRate_ms = t.read_us();
            t.reset();
        }
        else
        {
            motorEnable = 0;    // disable 3.3V source to motor driver
        }
        
        
    }

    return 0; 
}

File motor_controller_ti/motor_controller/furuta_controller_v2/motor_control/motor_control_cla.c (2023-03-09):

// Included Files
#include "cpu_cla_shared.h"
#include "epwm_global.h"
#include "dac_driver.h"


// Defines

#define CURRENT_SCALING (0.003076923077f)   // [A/adc_resolution] = (3/4095)*(5/2.976)*(1/0.4)
#define CURRENT_BIAS_LPF_A (1.6e-4f)    // 125ms time constant at 50kHz

#define TORQUE_CMD_LPF (0.01960f)  // 1kHz cutoff freq at 50kHz
#define TORQUE_CONSTANT (0.968f)    // [Nm/A]

#define CURRENT_CONTROLLER_KP (4.4257f)  // [V/A]
#define CURRENT_CONTROLLER_KI (4.4728f)  // [V/A] this term is already multiplied by the timestep (1e-5)
#define CURRENT_CONTROLLER_I_TERM_MAX (12.0f) // [V/A]

#define V_BRIDGE_MAX (12.0f)    // [V] DC voltage

#define MAX(a, b) __mmaxf32((a), (b))
#define MIN(a, b) __mminf32((a), (b))

#define SAT(x, max, min) (MAX(MIN((x), (max)), (min)))

// Globals
float pi_control_i_term;
float current_bias;
float torque_cmd_lpf;

// Private function declarations
static inline float get_current_feedback_from_adc(void);
static inline float accumulate_current_bias(const float current_val_raw, const bool enable);
static inline float pi_control(const float error);
static inline float calculate_duty_percent(const float v_bridge);
static inline void set_counter_compare_and_direction_pin(const float duty_percent, const bool enable, const float override_duty_percent, const uint16_t direction_override, const bool override_enable);

// CLA task
__interrupt void motor_torque_control(void)
{
    const float current_val_raw = get_current_feedback_from_adc();

    // Accumulate bias when current controller is not active
    const float current_feedback = accumulate_current_bias(current_val_raw, (!cla_inputs.enable) && (!cla_inputs.overrides_enable));

    torque_cmd_lpf += (cla_inputs.torque_cmd - torque_cmd_lpf) * TORQUE_CMD_LPF;

    const float current_ref = torque_cmd_lpf / TORQUE_CONSTANT;

    const float error = current_ref - current_feedback;

    const float v_bridge = pi_control(error);

    const float duty_percent = calculate_duty_percent(v_bridge);

    set_counter_compare_and_direction_pin(duty_percent, cla_inputs.enable, cla_inputs.override_duty_percent, cla_inputs.override_direction, cla_inputs.overrides_enable);

    // Set outputs
    cla_outputs.v_bridge = v_bridge;
    cla_outputs.duty = duty_percent;
    cla_outputs.current_feedback = current_feedback;

    dac_driver_set_value(DAC_BASE_A, current_ref, 6.0f);
}

// Private functions
static inline float get_current_feedback_from_adc(void)
{
    const int32_t adc_raw = AdcaResultRegs.ADCPPB1RESULT.all;   // post processing block already has the offset subtracted
    const float current_val_raw = adc_raw * CURRENT_SCALING;

    return current_val_raw;
}

static inline float accumulate_current_bias(const float current_val_raw, const bool enable)
{
    if(enable)
    {
        current_bias += (current_val_raw - current_bias) * CURRENT_BIAS_LPF_A;
    }

    const float current_val = current_val_raw - current_bias;

    return current_val;
}

static inline float pi_control(const float error)
{
    const float pi_control_p_term = error * CURRENT_CONTROLLER_KP;

    pi_control_i_term += error * CURRENT_CONTROLLER_KI;
    pi_control_i_term = SAT(pi_control_i_term, CURRENT_CONTROLLER_I_TERM_MAX, -CURRENT_CONTROLLER_I_TERM_MAX);
    pi_control_i_term = cla_inputs.enable ? pi_control_i_term : 0.0f;

    const float v_bridge = SAT((pi_control_p_term + pi_control_i_term), V_BRIDGE_MAX, -V_BRIDGE_MAX);

    return v_bridge;
}

static inline float calculate_duty_percent(const float v_bridge)
{
    const float duty_percent = SAT((v_bridge / V_BRIDGE_MAX), 1.0f, -1.0f);

    return duty_percent;
}

static inline void set_counter_compare_and_direction_pin(const float duty_percent, const bool enable, const float override_duty_percent, const uint16_t override_direction, const bool override_enable)
{
    if (override_enable)
    {
        const float override_duty_percent_saturated = SAT(override_duty_percent, 0.98f, 0.0f);
        const float counter_compare = MOTOR_CONTROL_TBPRD - (override_duty_percent_saturated * MOTOR_CONTROL_TBPRD);
        if (override_direction == 1U)
        {
            EPwm1Regs.CMPA.bit.CMPA = __mf32toui16r(counter_compare);
            EPwm1Regs.CMPB.bit.CMPB = MOTOR_CONTROL_TBPRD;
        }
        else
        {
            EPwm1Regs.CMPA.bit.CMPA = MOTOR_CONTROL_TBPRD;
            EPwm1Regs.CMPB.bit.CMPB = __mf32toui16r(counter_compare);
        }
    }
    else if (enable)
    {
        const float counter_compare = MOTOR_CONTROL_TBPRD - (fabsf(duty_percent) * MOTOR_CONTROL_TBPRD);
        if (duty_percent < 0.0f)
        {
            EPwm1Regs.CMPA.bit.CMPA = __mf32toui16r(counter_compare);
            EPwm1Regs.CMPB.bit.CMPB = MOTOR_CONTROL_TBPRD;
        }
        else
        {
            EPwm1Regs.CMPA.bit.CMPA = MOTOR_CONTROL_TBPRD;
            EPwm1Regs.CMPB.bit.CMPB = __mf32toui16r(counter_compare);
        }
    }
    else
    {
        EPwm1Regs.CMPA.bit.CMPA = MOTOR_CONTROL_TBPRD;
        EPwm1Regs.CMPB.bit.CMPB = MOTOR_CONTROL_TBPRD;
    }
}


__interrupt void sw_task(void)
{
    // initialize global variables
    pi_control_i_term = 0.0f;
    current_bias = 0.0f;
    torque_cmd_lpf = 0.0f;
}

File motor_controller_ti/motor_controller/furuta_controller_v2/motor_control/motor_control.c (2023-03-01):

/*
 * motor_control.c
 *
 *  Created on: 11-Dec-2022
 *      Author: Samvrit
 */

#include "motor_control.h"
#include "epwm_global.h"
#include "cpu_cla_shared.h"

#include "driverlib.h"
#include "device.h"

void motor_control_init(void)
{
    GPIO_writePin(122, 1U); // enable

    cla_inputs.enable = false;
    cla_inputs.override_direction = 0;
    cla_inputs.overrides_enable = false;
    cla_inputs.override_duty_percent = 0.0f;
    cla_inputs.torque_cmd = 0.0f;
}

void motor_control_motor_enable(void)
{
    GPIO_writePin(122, 1U);
}

void motor_control_motor_disable(void)
{
    GPIO_writePin(122, 0U);
}

void motor_control_fault_reset(void)
{
    GPIO_writePin(122, 1U);

    DEVICE_DELAY_US(25U);

    GPIO_writePin(122, 0U);

    DEVICE_DELAY_US(25U);

    GPIO_writePin(122, 1U);
}

float motor_control_get_current_fb(void)
{
    return cla_outputs.current_feedback;
}

float motor_control_get_v_bridge(void)
{
    return cla_outputs.v_bridge;
}

float motor_control_get_duty_ratio(void)
{
    return cla_outputs.duty;
}

float motor_control_get_torque_cmd(void)
{
    return cla_inputs.torque_cmd;
}

void motor_control_set_enable(const uint16_t enable)
{
    cla_inputs.enable = enable;
}

void motor_control_set_override_enable(const uint16_t enable)
{
    cla_inputs.overrides_enable = enable;
}

void motor_control_set_override_duty_ratio(const float duty)
{
    cla_inputs.override_duty_percent = duty;
}

void motor_control_set_override_direction(const uint16_t direction)
{
    cla_inputs.override_direction = direction;
}

void motor_control_set_torque_cmd(const float torque_cmd)
{
    cla_inputs.torque_cmd = torque_cmd;
}

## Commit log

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2019-10-24 separate the network thread
2019-10-26 ls in current path
2019-10-28 add example files for SPI transfer
2019-10-29 add code for SPI transfer
2019-10-29 SPI data sending over WiFi working
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2020-02-27 tune PID for motor
2020-03-07 matlab: create transfer function model of arbitrary motor
2020-03-07 solids: add solid models
    [bearing-6mm.SLDPRT, bearing-mount-1.SLDPRT, bearing.SLDPRT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]
2020-03-07 solids: add motor mount
    [mount-motor.SLDPRT]
2020-03-09 solids: create subassemblies
    [Assembly_base.SLDASM, Assembly_link1.SLDASM, Assembly_link2.SLDASM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]
2020-03-09 solids: create complete model and export to matlab
    [Assembly_base.SLDASM, Assembly_link1.SLDASM, Assembly_link2.SLDASM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]
2020-03-09 solids: create matlab model
    [bearing-6mm_Default_sldprt.STL, bearing-mount-1_Default_sldprt.STL, bearing_Default_sldprt.STL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]
2020-03-14 mbed: setup working PWM
2020-03-15 motor: write pwm to motor
2020-03-16 motor: setup enable button for mosfet
2020-03-17 mbed: setup ADC and increase baud rate
2020-03-18 motor: write PI control loop
2020-03-18 motor: implement torque control
2020-03-19 motor: move low pass filter and saturate functions to macros and reduce default baud rate
2020-03-20 motor: get Serial working
2020-03-21 motor: get uart to work
2020-03-21 motor: add motor enable pin
2020-03-22 motor: swap pins, change lower and upper duty cycle bounds
    [main.cpp]
2020-03-22 motor: change Kp Ki values
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2020-03-23 motor: use absolute value for torque error signal
    [main.cpp]
2020-03-23 motor: add outer brackets for LPF macro
2020-03-23 motor: use macro for absolute value
2020-03-23 motor: increase cutoff frequency for low pass filter
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2020-03-24 motor: add test for calculating damping coeffiecient
2020-03-24 motor: make comment clearer
2020-03-24 motor: print only when enabled
2020-03-25 motor: add analog input for measuring back emf
2020-03-27 motor: clean up code, disable irq during packet processing, use memcpy instead of for loop, rename variables
2020-03-27 motor: change printf statement
2020-03-28 motor: fix bugs
2020-03-28 motor: use absolute value for current after correcting for offset
    [main.cpp]
2020-03-28 motor: use macro to define pwm frequency
2020-03-28 motor: saturate current sense value
2020-03-28 motor: only print when motor enabled
2020-03-28 motor: increase PWM freq to 20kHz and comment out printf statement
2020-03-30 motor: change PI gains and remove printf statement
2020-03-30 motor: add code for reading motor speed, but don't use just yet
2020-03-31 motor: configure board to use clock from ST-Link, and implement speed limit
2020-04-01 motor: configure mbed to use only HSI, and compute motor speed
2020-04-01 Matlab/system model (#19)
    * matlab: fix dh parameters to suit simulink's error in z-axis translation from solidworks and build basic working model
    * matlab: add logging and saturation for torque
    * matlab: add Kt calculation from experimental data in motor model
    * matlab: add transfer function as calculated from picoscope data
    * matlab: use data from experiment for motor transfer function
    * make motor block an LTI block instead of a subsystem
    * matlab: obtain back emf constant through experiment and use in model
    * matlab: add motor model to system simulation
    * matlab: modify damping constant by adjusting speed by gearbox ratio
    * matlab: model measurement noise
    *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
    [backemf_data.csv]
2020-04-01 add scripts folder with script for sending torque commands over serial
2020-04-03 add code composer studio folder for motor controller code
2020-04-07 ti: add relevant examples to workspace
    [F2837xD_CodeStartBranch.obj, asin.obj, cla_ex1_asin.obj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]
2020-04-07 ti: merge PWM and ADC SOC code
2020-04-07 ti: merge sci to adc code
2020-04-08 ti: merge CLA code with ADC, SCI, PWM
    [F2837xD_CodeStartBranch.obj, asin.obj, cla_ex1_asin.obj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]
2020-04-08 ti: clean up comments and remove unused example code
    [F2837xD_CodeStartBranch.obj, device.obj, interrupt_ex1_external.obj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]
2020-04-09 ti: add code for GPIO for motor driver and external interrupt for switch
2020-04-10 ti: add code for eqep module
    [F2837xD_CodeStartBranch.obj, device.obj]
2020-04-10 ti: add sleep pin for motor driver
    [device.obj]
2020-04-12 ti: add speed threshold
    [device.obj]
2020-04-12 ti: remove example files
    [eqep_ex1_calculation.xls]
2020-04-12 ti: remove unwanted files and change motor direction
2020-04-16 matlab: fix transfer function, frictional damping coefficient, and make the reference tracking awesome!
    [backemf_data.csv]
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2020-04-19 matlab: add motor plant noise
2020-04-20 add pull up config to interrupt pin
    [device.obj]
2020-04-24 matlab: add MIA signal to kalman filter block
2020-04-27 ti: move cla functions to CPU1
    [device.obj]
2020-04-28 ti: make direction dependent on error signal
    [main.c]
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2020-05-04 ti: add max and min adc value variables
    [device.obj]
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2020-05-08 solids: modify mount-top
    [mount-top.SLDPRT]
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2020-05-09 arduino: get angle to work correctly
    [Esp32UDPClient.ino]
2020-05-16 ti: fix current sensor bias
    [device.obj]
2020-06-08 solids: modify motor mount to accommodate alternate motor
    [Assembly_base.SLDASM, Complete_assembly.SLDASM, mount-motor.SLDPRT]
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2020-07-20 add wireless PCB design
    [WirelessPCB-Micro.SchDoc, WirelessPCB.PrjPCB]
2020-10-31 matlab: characterize pololu motor
    matlab: get baseline kalman filter working with 500us cycle time
    matlab: add script to calculate kalman gain
    matlab: vary initial angles and test Kalman filter's efficiency
    Get kalman filter script working
    ti: add build configurations instead of macros
    ti: add paranthesis for macro
    ti: clean up code and move interrupts to seperate file
    ti: add SPI GPIO config
    ti: get SPI working
    ti: add dsp library and make interrupts short
    ti: get SPI to work with ESP32
    ti: correct bit rate and add SPIB GPIO configs
    ti: use pragma unroll for for loop
    ti: remove redundant timer code
    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
    [WirelessPCB-Micro.SchDoc, WirelessPCB.PrjPCB, device.obj]
2021-04-04 Add discrete simulation
    Add transport delay
    Increase process variance
    tighten LQR gain for X4
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2022-11-19 First order approximation of motor; move old models and scripts to different directory and remove generated files from version control
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2022-11-30 Add framework for kalman filter in the TI controller
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2022-12-11 Working SPI comms with RLS after removing caps
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2022-12-25 Add code for IO0 interrupt and CCW command for MPS
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2022-12-28 Use semaphores and queues and timers and stuff
2022-12-30 Add component folder for MPS comms and calibration works well
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2022-12-30 Correct scaling for ESP angles
    [esp_comms.c]
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2023-01-10 Change ESP SPI word length to 14 bits
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2023-02-20 Use complementary PWM for DRV8256P and bring up DAC driver
2023-02-21 Make SCI interrupt at 5 chars and add GUI stuff for motor control
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2023-02-26 Add function to write signals to file and add reset motor button
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2023-03-10 Add high pass filter to x_hat0 and enable interface to posteriori in kalman filter
2023-03-10 Set torque and enable commands from core controls
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2023-03-29 Add two link model
    [bearing-6mm_Default_sldprt.STL, bearing-mount-1_Default_sldprt.STL, bearing_Default_sldprt.STL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]
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2023-05-02 Remove ramfuncs which fixes ESP comms
    [core_controls.c, esp_comms.c]
2023-06-18 Add motor torque control model and slight modification to double pendulum state machine
